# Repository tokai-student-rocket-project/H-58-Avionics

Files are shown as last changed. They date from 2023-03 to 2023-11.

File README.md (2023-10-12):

# H-58 搭載計器





TSRP-H-58に搭載する計器類のプログラム及び設計書を保存するレポジトリです。

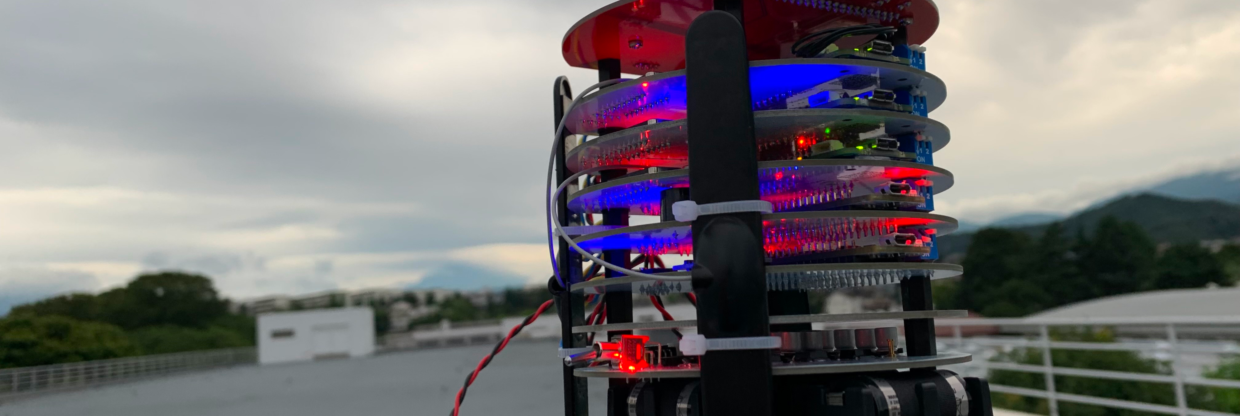
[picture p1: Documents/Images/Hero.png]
Hero


## はじめに

学生ロケットの電装系を盛り上げたい思いから、全てのソースコードを含む設計を公開しています。ガバガバ開発ですので、分かりにくい点（資料がまとまっていないなど）が多々あります。ご了承ください。

ご不明な点は以下のSNSからお気軽にお問合せください。

- X (旧Twitter): [@Tokai_SRP](https://twitter.com/Tokai_SRP)

### 計器の概要

H-58搭載計器はCANBUS接続された複数のモジュールから構成されます。

### レポジトリ構成

#### ./Components/Modules/

- [SystemDataCommunicationModule](./Components/Modules/SystemDataCommunicationModule/README.md)  
- [AirDataCommunicationModule](./Components/Modules/AirDataCommunicationModule/README.md) 
- [FlightModule](./Components/Modules/FlightModule/README.md)  
- [SensingModule](./Components/Modules/SensingModule/README.md) 
- [ValveControlModule](./Components/Modules/ValveContolModule/README.md) 
- [MissionModule](./Components/Modules/MissionModule/README.md) 
- [PowerModule](./Components/Modules/PowerModule/README.md) 

#### ./Documents/

- 開発資料
  - [工程計画書](./Documents/Materials/Schedule.md)
  - [要件定義書](./Documents/Materials/RequirementsDocument.md)
  - [基本設計書](./Documents/Materials/BasicDesignDocument.md)
  - [詳細設計書](./Documents/Materials/DetailedDesignDocument.md)
- 安全審査
  - [一次審査(Z-storage)](https://docs.google.com/document/d/1F-2k9H3952sz7PHYDDPXtUgwHEACfZ0U/edit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)
  - [二次審査(Z-storage)](https://drive.google.com/file/d/1VNDg2A9r9_NxHciDonn3Oh5dWTKx7AV1/view?usp=sharing)
- マニュアル
  - [部品一覧](./Documents/Materials/Manual/PartsList.md)
  - 手順書
    - [組み立て手順書](./Documents/Materials/Manual/Procedure/AssemblyProcedure.md)
- [詳細報告書](./Documents/Reports/DetailedRaport.pdf) (一番情報量多い)

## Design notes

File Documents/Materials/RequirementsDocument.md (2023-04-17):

# 要件定義書

H-58 搭載計器の要件定義、及びシステムの概要について記載する。

## 概要

### 要件

- 海打ち 2 段階分離に対応
- ±200g, 1kHz の加速度計測
- 熱電対による充填確認
- 統合システムとデータバスの実証
- 高速ダウンリンクの実証

### システム構成

- Nucleo-STM32F303K8
- CAN-BUS
- 計測系
  - 加速度/ジャイロ/地磁気
  - クオータニオン
  - 線形加速度
  - 姿勢角
  - 高 g 加速度
  - 気圧
  - 気温
  - 電圧
  - GNSS
- データ処理系
  - 速度算出
  - 高度算出
  - 出力
    - SD カード
    - EEPROM
- 制御系
  - バルブ制御
  - 分離制御
  - フライトモード
  - 状態検知
    - リフトオフ検知
    - 燃焼終了検知
    - 頂点検知
    - 開傘検知
    - 着地検知
- 通信系
  - 1kHz ダウンリンク
  - 慣性情報ダウンリンク
  - 高度情報ダウンリンク
  - 制御情報ダウンリンク
  - 汎用アップリンク
- 電源系
  - 12V パワーライン
  - 5V パワーライン
  - 電池ボックス
  - 変圧基板
  - 12V バルブ電源
- 構造系
  - 計器タワー
  - 水密
  - THR 制御モジュール
  - 搭載カメラ

## モジュール

従来の共通計器, テレメータの統合を行い、各機能をモジュールとして分割して開発を行う。

システムを構成するモジュールは以下の通りである。

- 計測モジュール
- 飛翔管理モジュール
- 通信モジュール
- THR 制御モジュール

各モジュールはプロセッサとして Nucleo-STM32F303K8 を積む。また、各モジュールは CAN-BUS を通して通信を行う。

CAN-BUS を使用したモジュール式のシステムとすることで、高い拡張性と疎結合による高い運用性を期待できる。

Nucleo-STM32F303K8 のマイコンである STM32F303 は、H-57 に搭載した Arduino MKR WAN 1310 の ATSAMD21 と比較して特段性能が高いわけではないが、より高性能なマイコンを有する STM シリーズの開発運用経験を蓄積することができる。これに加えて、ATSAMD21 と STM32F303 は同じ ARM コアであるため、プログラムの互換性があり学習コストが低く、Arduino から STM のステップアップとして最適であると考える。

| | ATSAMD21 | STM32F303 |
| --- | --- | --- |
| 動作周波数 | 48MHz | 72MHz |
| ビット数 | 32bit | 32bit |
| コアの数 | シングルコア | シングルコア |
| コアの種類 | ARM® Cortex®-M0+ | ARM® Cortex®-M4 |
| Flash サイズ | 256kB | 64kB |
| RAM サイズ | 32kB | 16kB |
| 接続性 | I²C, LINbus, SPI, UART/USART, USB | CANbus, I²C, IrDA, LINbus, SPI, UART/USART |

## 計測系

GNSS は通信モジュールで行われ、それ以外は計測モジュールで計測する。

計測するデータと計測レートは以下の通りである。

なお、クオータニオン, 線形加速度, 姿勢角はセンサ内で算出される(NDOF=NineDegreesOfFreedom)ため、計測系として扱う。

また、出力データはデータ処理系に送り、SD, EEPROM に保存されるほか、通信系に送りダウンリンクする。

| データ | センサ | レート | 出力先 |
| --- | --- | --- | --- |
| 加速度 | BNO055 | 100Hz  | SD, ダウンリンク |
| ジャイロ | BNO055 | 100Hz  | SD, ダウンリンク |
| 地磁気 | BNO055 | 100Hz  | SD, ダウンリンク |
| クオータニオン | BNO055 (NDOF)  | 100Hz  | SD, ダウンリンク |
| 線形加速度 | BNO055 (NDOF)  | 100Hz  | SD, ダウンリンク |
| 姿勢角 | BNO055 (NDOF)  | 100Hz  | SD, ダウンリンク |
| 高 g 加速度 | ADXL375 | 1kHz | EEPROM |
| 気圧 | LPS33HW | 100Hz  | SD, ダウンリンク |
| 気温 | サーミスタ ADC | 2Hz | SD, ダウンリンク |
| 電圧 | ADC | 10Hz | SD, ダウンリンク |
| GNSS | SAM-M8Q | 10Hz | SD, ダウンリンク |

## データ処理系

主に計測系で得たデータを処理する。

### 速度算出

線形加速度を経過時間で積分することで求める。

### 高度算出

計測した気圧と気温、及び打ち上げ前に設定する海面気圧から求める。

### 出力

計測や算出した値は以下の 3 通りの出力先に送信される。

- SD
- EEPROM
- ダウンリンク

基本的に全てのデータを SD に保存するとともに、通信系からダウンリンクで地上に送信する。
海打ちの H-58 では、水没や損傷によるデータロストを防ぐためにダウンリンクに重点を置いている。

高 g 加速度のみ計測レートが大きいため EEOROM に保存する。EEPROM は海打ちで実質弾道落下となり水没した H-49 でもデータの保持に成功している。

データの出力に必要な通信速度は以下の通りである。

| 出力先 | 通信速度  |
| --- | --- |
| SD | 38.4 kbps |
| EEPROM | 48 kbps |
| ダウンリンク | 38.4 kbps |

なお、通信速度は値を符号なし 8bit 整数 2 つとみて、生のまま送信した場合である。実際は、パケットに Id や CRC が含まれるため、さらに通信速度は必要になる。

ダウンリンクはデータが経由する CAN-BUS と LoRa でそれぞれ必要になる通信速度である。

## 制御系

制御系はバルブ制御と分離制御、内部制御用のフライトモードと状態検知からなる。

### バルブ制御

THR 制御モジュールで行い、GSE のバルブ開閉信号を受信してバルブシステムのサーボモータを制御する。
サーボモータの制御には RS485 通信を使う。

### 分離制御

不知火の電磁弁に分離信号の DC12V を供給することで分離させる。
H-58 では 2 段階分離となるため、不知火 Ⅲ を頂点、不知火 Ⅳ を指定高度で動作させる。

## 通信系

LoRa による搭載計器地上局間の通信を 5 系統用意する。そのうち 2 系統はダウンリンク用、1 系統はアップリンク用である。

通信モジュールのみプロセッサに Nucleo-STM32F303K8 ではなく Arduino MKR WAN 1310 を使用する。

### 1kHz ダウンリンク

燃焼中3秒間程度の1kHz加速度情報を1分程度かけてダウンリンクする

### 慣性情報ダウンリンク

BNO055から出力される慣性データをダウンリンクする

### 高度情報ダウンリンク

気圧や気温、算出された高度データをダウンリンクする

### 制御情報ダウンリンク

フライトモードやステータスなどの制御情報をダウンリンクする

### 汎用アップリンク

地上局からのコマンドを受信する

## 電源系

### 12V パワーライン

Nucleo-STM32F303K8 は VIN に 12V を受け付けるため、電池ボックスが出力する 15V を変圧基板で 12V へ変圧して各モジュールに供給する。

### 5V パワーライン

Arduino MKR WAN 1310 と搭載カメラを制御する Raspberry Pi は駆動に 5V を要するため、変圧基板で 5V へ変圧して供給する。

### 電池ボックス

3V 出力が可能な CR123A を 5 個直列接続して 15V 出力の電池ボックスとする。電池容量が不足する場合は、電池ボックスを並列接続する。

### 変圧基板

複数個の 3 端子レギュレータで電池ボックスが出力する 15V を 12V と 5V に変圧する。

12V パワーラインと 5V パワーラインは外部給電を設けずに、電源投入時にスイッチで電池ボックスと変圧基板を接続する。

### 12V バルブ電源

バルブ駆動用電源は別系統として、外部給電を行う。内部電源と外部電源は THR 制御モジュール内で切り替える。

## 構造系

### 計器タワー

衝撃に耐えるために、スペーサーを上下のカプラに接続する蓋で固定する両端固定梁の構造とする。
上下の蓋は従来のベークライトではなく、ガラスエポキシを試す。

### 水密

機体チューブの 1 重構造として、上下のカプラ部分に防水用の構造を取り付ける。

### THR 制御モジュール

バルブ制御は燃焼関係の計測を行う THR 制御モジュールの基板は計器タワーではなくバルブ付近に搭載する。

### 搭載カメラ

機体外を撮影するカメラを搭載する。カメラには Raspberry Pi のカメラモジュールを使用する。

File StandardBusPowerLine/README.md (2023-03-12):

# 標準バスパワーライン

ケーブルとコネクタを定めた接続規格です。モジュールの接続に使用します。

## ケーブル

9VとGNDの電源対、CAN_HとCAN_Lの信号対からなる4線2対のツイストケーブルを使用します。

## コネクタ

※未定

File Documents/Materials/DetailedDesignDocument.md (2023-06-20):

# 詳細設計書

## 基本設計からの変更点

- 状態確認用のブザーを追加
- [タイマーのコンフィグについて追記](#フライトモード-フライトモジュール)
- [ロジック図を追加](#分離制御-フライトモジュール)
- [アップリンクの誤動作対策を追加](#システムデータ通信モジュール)
- [計器チューブの穴の寸法を追記](#計器チューブ穴寸法)
- [機体間通信実証モジュールを追加](#機体間通信実証モジュール)
- [バルブ制御モジュールを追加](#アクチュエーターバルブ制御モジュール)
- [THR制御モジュールを削除](#機体間通信実証モジュール)

## 概要

### 特徴

#### 新規要素

- モジュール式の統合システム
- データバスの採用
- ±200g, 1kHz の加速度計測
- 熱電対による充填確認
- クオータニオンのリアルタイム算出

#### 強化要素

- Arduinoからステップアップした高性能マイコン
- 表面実装による小型化
- ダウンリンクの速度向上
- GPS取得頻度向上
- 配線の簡略化による運用性向上

#### 修正要素

- 点火前からの計測
- 外気温計測
- 頂点検知の感度調整

### 成功基準
<!-- 特徴毎に成功基準を設定（通信, ○○制御など） -->

| ミッション | ミニマムサクセス | フルサクセス | エクストラサクセス  |
| :---: | :---: | :---: | :---: |
| フライトモード | フライトピン開放で計測開始 | バルブ開信号で計測開始 | コマンドで計測開始  |
| 分離制御 | 強制分離 (タイマー) | 精度向上のための制御情報取得 | 頂点分離 (頂点検知) |
| 1kHz加速度 | 750Hz~で計測 | ダウンリンクの遅延送信 | OPSの計測 |
| 電源系統 | 安定した電力供給 | バッテリー残量の遠隔監視 | 正常な電源切替 |
| 通信系統 | ダウンリンクの受信 | 2Hz以上で受信 | 10Hz以上で受信 |

## システム
<!-- モジュール同士のデータ的な接続をシステム系統図で説明 -->

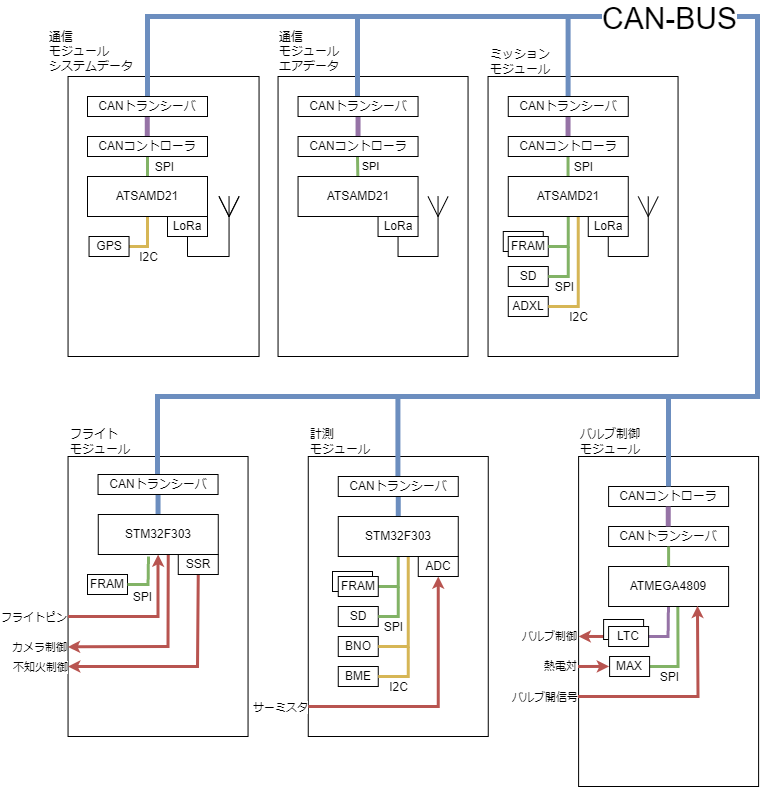
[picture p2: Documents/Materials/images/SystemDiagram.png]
SystemDiagram


### モジュール

従来の共通計器, テレメータの統合を行い、各機能をモジュールとして分割して開発を行う。

システムを構成するモジュールは以下の通りである。

- 計測モジュール ... データ計測, 算出, 保存
- フライトモジュール ... フライトモード管理, 分離制御
- 通信モジュール
  - エアデータ ... 慣性情報, 高度情報のダウンリンク
  - システムデータ ... 制御情報, GNSS情報のダウンリンク, コマンドのアップリンク
- ミッションモジュール ... 1kHz加速度情報の計測, 保存, ダウンリンク
- バルブ制御モジュール ... バルブ制御, 充填確認
- 機体間通信実証モジュール ... CAN通信, 温度

各モジュールはSTM32F303, ATSAMD21, ATSAMD11D14A, ATMega4809のいずれかをマイコンとして搭載しICを介してCAN-BUSに接続する。

### データバス
<!-- CAN-Busの採用とその効果を説明 -->

モジュール間のデータ的な接続のためにCAN-BUSを採用した。CAN-BUSは自動車で広く一般的に使われているデータ通信プロトコルである。通信速度は1Mbpsと必要十分であり、差動式信号のためノイズへの高い耐性を持つ。

データバスの採用により従来の煩雑な配線を減らし、拡張性の高いシステムを構成することができる。また、モジュール間は疎結合となることで、モジュールの開発が容易になり運用性の向上も期待できる。

### データフロー
<!-- データフロー図で説明 -->

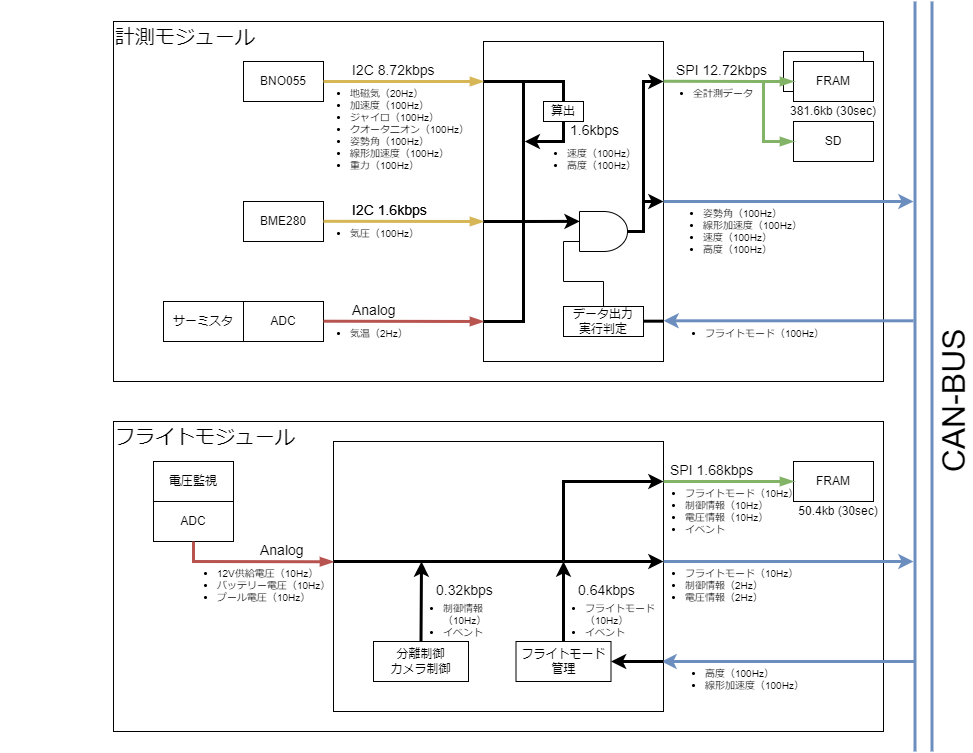
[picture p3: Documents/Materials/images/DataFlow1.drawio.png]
DataFlow1


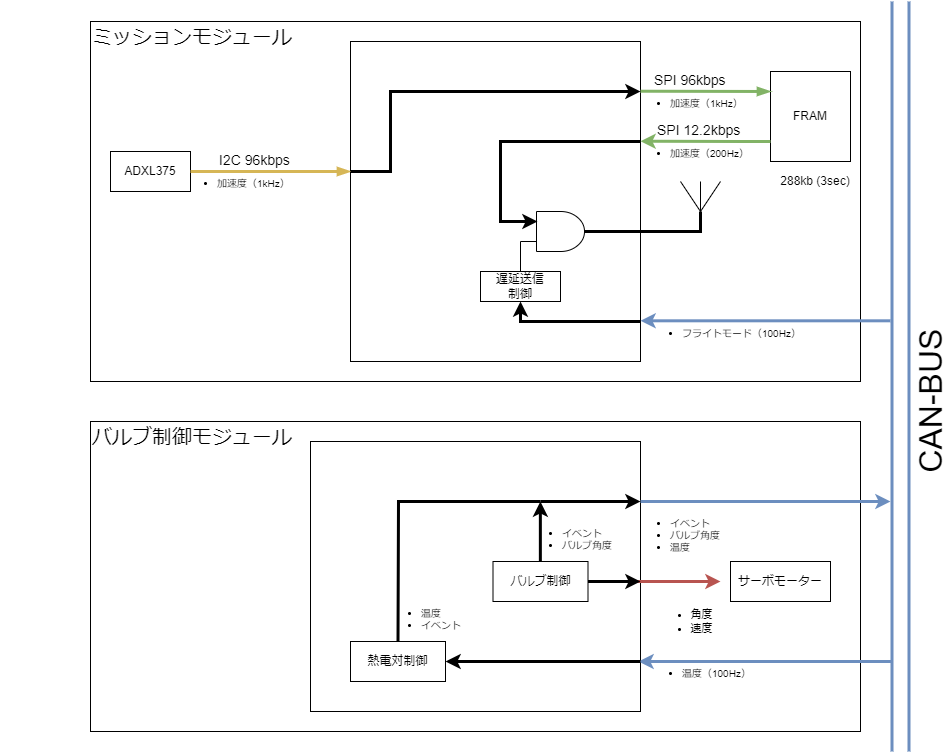
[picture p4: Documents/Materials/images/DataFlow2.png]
DataFlow2


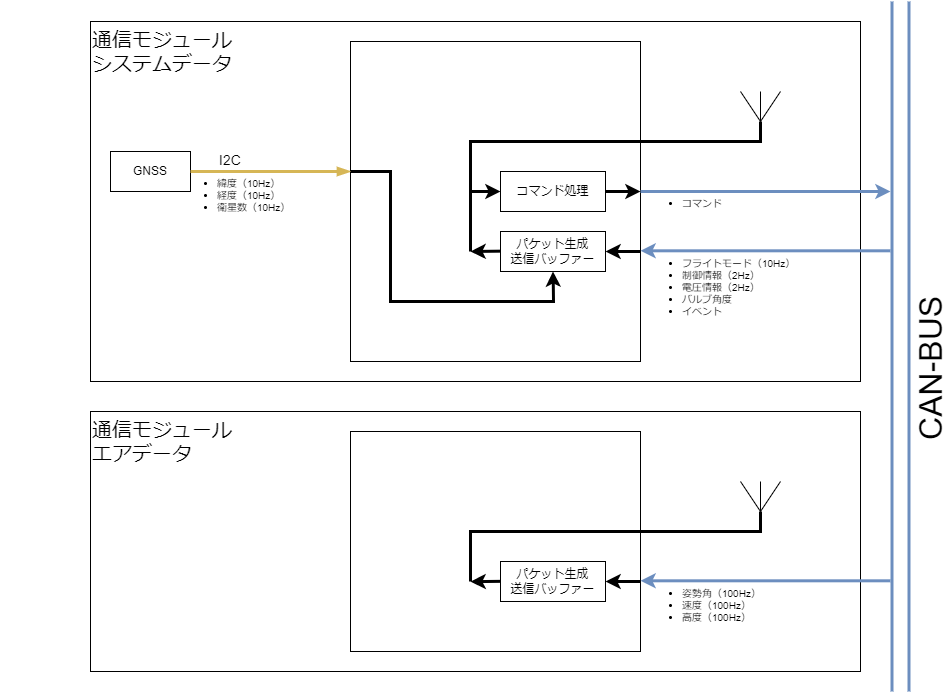
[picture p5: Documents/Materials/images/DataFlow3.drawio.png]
DataFlow3


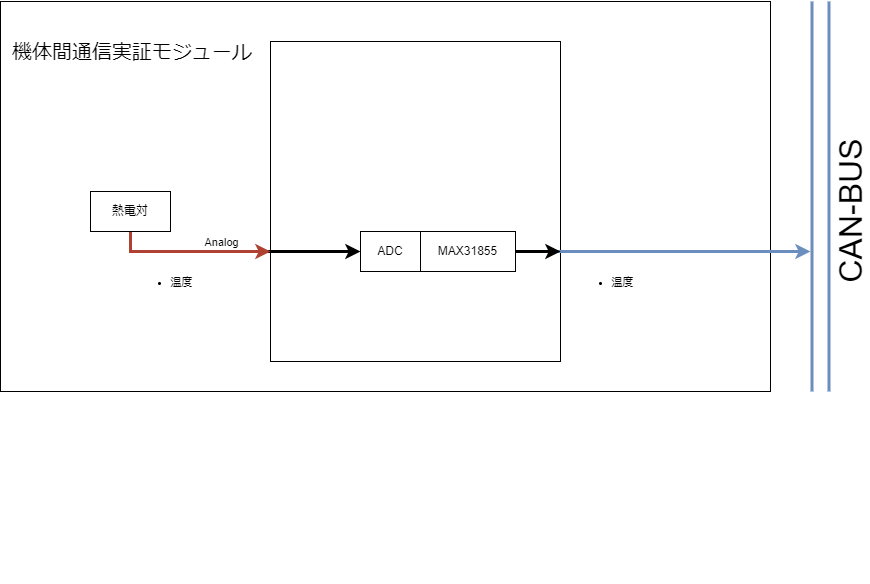
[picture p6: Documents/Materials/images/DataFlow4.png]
DataFlow4


### 電気系統
<!-- 外部給電を含めて電源系統図で説明 -->

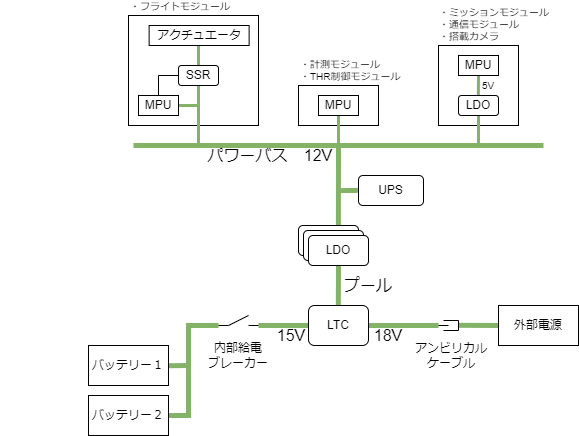
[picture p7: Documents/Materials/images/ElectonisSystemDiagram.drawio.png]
ElectonisSystemDiagram


## 機能

### 計測系

データ保存にはFRAM (Fujitsu MB85RS2MT) とマイクロSDカードを使用する。海打ち仕様として、着水時にFRAMとSDを電気的に遮断することでショートを防止する機構を搭載する。

データ保存はフライトモードオンのタイミングより開始する。 (概ね点火5~10秒前)

#### GNSS情報 (システムデータ通信モジュール)

| データ | センサ  | 出力レート | 出力先 | データ型 | 通信速度 |
| --- | --- | --- | --- | --- | --- |
| 緯度 | SAM-M8Q | 10Hz | ダウンリンク | float | 320bps |
| 経度 | SAM-M8Q | 10Hz | ダウンリンク | float | 320bps |
| 衛星数 | SAM-M8Q | 10Hz | ダウンリンク | int16_t  | 160bps |

#### 慣性情報 (計測モジュール)

| データ | センサ | 出力レート | 出力先 | データ型 | 通信速度 |
| --- | --- | --- | --- | --- | --- |
| 加速度 | BNO055 | 100Hz | FRAM, SD | float * 3axis | 9.6kbps  |
| ジャイロ | BNO055 | 100Hz | FRAM, SD | float * 3axis | 9.6kbps  |
| 地磁気 | BNO055 | 20Hz | FRAM, SD | float * 3axis | 1.92kbps |
| クオータニオン | BNO055 (NDOF) | 100Hz | FRAM, SD | float * 4axis | 12.8kbps |
| 姿勢角 | BNO055 (NDOF) | 100Hz | FRAM, SD, ダウンリンク | float * 3axis | 9.6kbps  |
| 線形加速度 | BNO055 (NDOF) | 100Hz | FRAM, SD, ダウンリンク, 制御系 | float * 3axis | 9.6kbps  |
| 重力 | BNO055 (NDOF) | 100Hz | FRAM, SD | float * 3axis | 9.6kbps  |
| 速度 | 算出 | 100Hz | FRAM, SD, ダウンリンク | float * 3axis | 9.6kbps  |

#### 高度情報 (計測モジュール)

| データ | センサ | 出力レート | 出力先 | データ型 | 通信速度 |
| --- | --- | --- | --- | --- | --- |
| 気圧 | BME280 | 100Hz | FRAM, SD | float | 3.2kbps  |
| 気温 | サーミスタ | 2Hz | FRAM, SD | float | 64bps |
| 高度 | 算出 | 100Hz | FRAM, SD, ダウンリンク, 制御系 | float | 3.2kbps  |

#### 1kHz加速度 (ミッションモジュール)

| データ | センサ  | 出力レート | 出力先 | データ型 | 通信速度 |
| --- | --- | --- | --- | --- | --- |
| 加速度 | ADXL375 | 1kHz | FRAM, ダウンリンク | float * 3axis | 96kbps |

#### 電圧監視 (フライトモジュール)

12V供給, バッテリー電圧, プール電圧を監視する。これにより、遠隔で電池残量の推測や電源の切替状況を監視することができる。

正常値の監視電圧を分圧回路により2.4Vに降圧した後、ADCで電圧を読み取る。これに係数を乗ずることで元の電圧を取得する。

#### 充填監視

| データ | センサ | 出力レート | 出力先 | データ型 | 通信速度 |
| --- | --- | --- | --- | --- | --- |
| 温度 | MAX31855 | 500Hz | ダウンリンク | float | 3.2kbps |

### 制御系

#### フライトモード (フライトモジュール)

状態をフライトモードで管理する。既定の条件を満たすことで次のモードに遷移する。モード遷移時にイベントを発行してダウンリンクで送信する。

バックアップとしてのタイマーはシミュレーションの結果を元に決定する。したがって、打ち上げ当日の早朝と打ち上げ直前に以下のコンフィグをシミュレーション担当と共に作成する。

| | 備考 | H-57の時間(参考) |
| --- | --- | --- |
| モータ作動時間 | | 2,110 ms |
| 分離保護時間 | モータ作動時間からマージン かつ 頂点到達数秒前以内 | 8,196 ms |
| 強制分離時間 | パラが耐えられる対気速度 かつ 頂点到達数秒後以内 | 9,959 ms |
| 着地時間 | 減速落下の場合の時間 | 38,659 ms |
| シャットダウン時間 | 着地時間の数秒程度後 | 43,649 ms |

頂点一段階分離では頂点検知により直接Parachuteモードへ遷移するため、DescentモードとDecelモードは飛ばされる。

| モード | 遷移条件 | 動作 | 備考 |
| --- | --- | --- | --- |
| Sleep | 電源投入 | なにもしない, コマンドは受け付ける | |
| Standby | WakeUpコマンド or Launch信号 (通信不可時) | 計測開始 | フライトモードオン |
| Thrust | 離床検知 | タイマ開始 | |
| Climb | 想定モータ作動時間 | マージン後頂点検知許可 (分離保護時間) | |
| Descent | 頂点検知 | すぐにDecelへ遷移 (頂点分離) | 頂点分離では実質飛ばされる |
| Decel | タイマー (一段目強制分離時間) or 緊急分離コマンド | 一段目分離 | ドローグシュート展開 |
| Parachute | 指定高度到達 or タイマー (二段目強制分離時間) | 二段目分離 | メインシュート展開 |
| Land | タイマー (想定着地時間) | | |
| Shutdown  | タイマー (シャットダウン時間) | 計測終了 | |

#### 離床検知 (フライトモジュール)

フライトピンの離脱による回路切断をプルアップ入力で検知する。チャタリング対策には従来のソフトウェア実装からハードウェア実装に変更した。これにより、発生する遅延を10ミリ秒から2ミリ秒に短縮した。

| 対策前 | 対策後 |
| :---: | :---: |
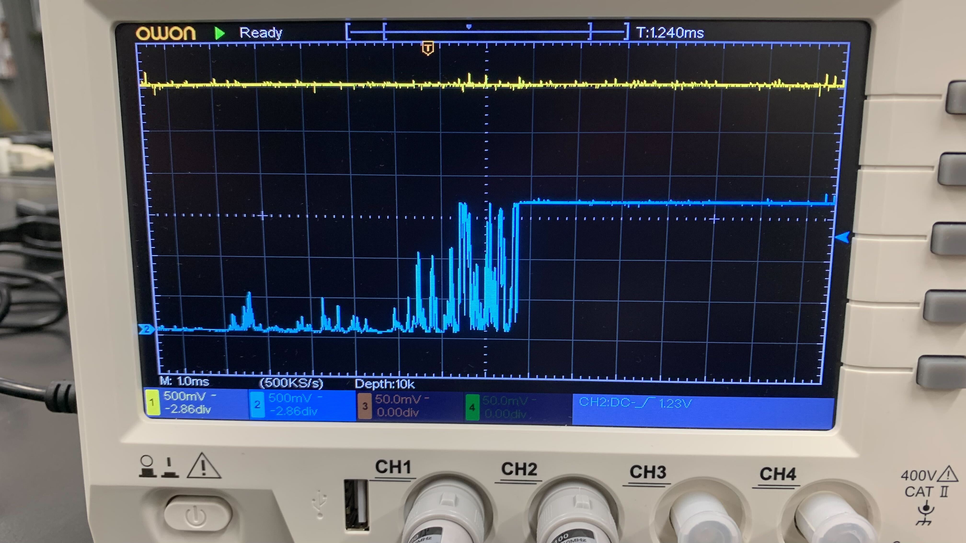
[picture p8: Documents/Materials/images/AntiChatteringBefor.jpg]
AntiChatteringBefor
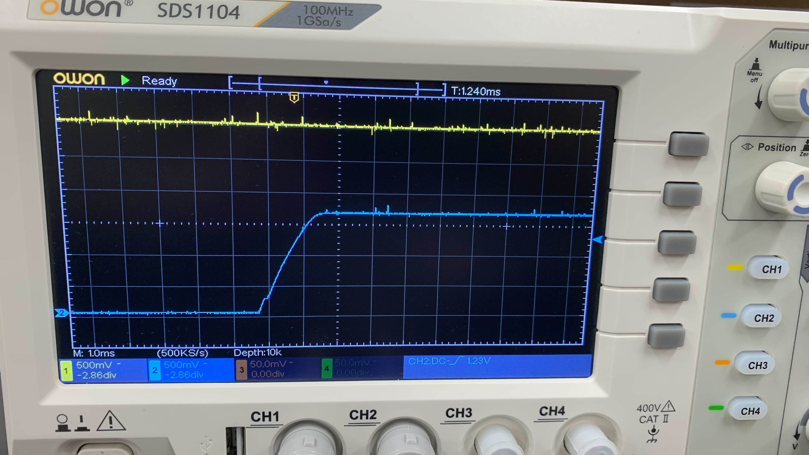
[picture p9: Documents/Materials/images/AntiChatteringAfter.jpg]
AntiChatteringAfter
|  |  |

以下にチャタリング除去回路を示す。

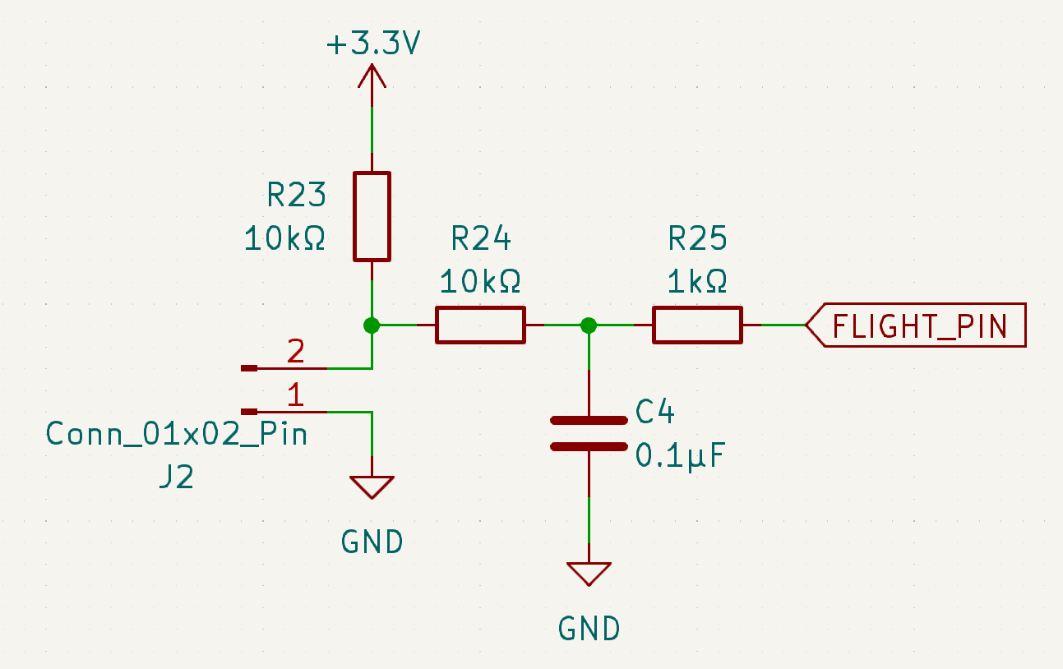
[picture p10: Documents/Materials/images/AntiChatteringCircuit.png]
AntiChatteringCircuit


#### 頂点検知 (フライトモジュール)

H-57で得た改善モデルにより、平滑化定数を0.5とした指数移動平均によって平滑化した高度変化が5回連続で減少したことを検知する。

頂点検知のロジックを以下に示す。

ApogeeDetectionLogic

以下にH-57のフライトデータを例にした頂点検知を示す。初めに連続降下回数を閾値が越えたX+9.57秒後 (実際の頂点到達の0.35秒後) に頂点検知が行われることがわかる。

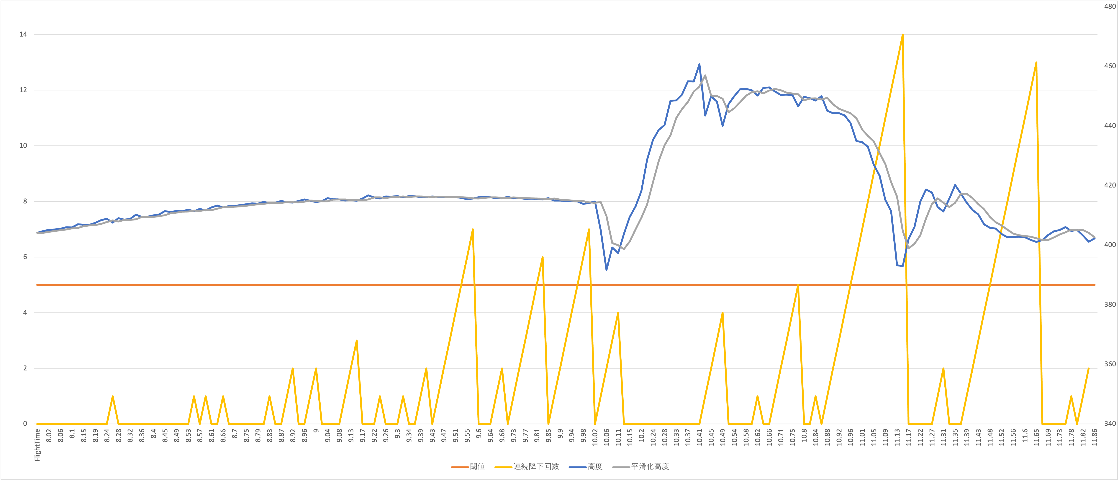
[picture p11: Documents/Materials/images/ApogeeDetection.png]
ApogeeDetection


#### 分離制御 (フライトモジュール)

頂点検知による頂点分離及び、バックアップとしてタイマーによって分離信号を出す。

離床を含めた分離制御のロジックを以下に示す。

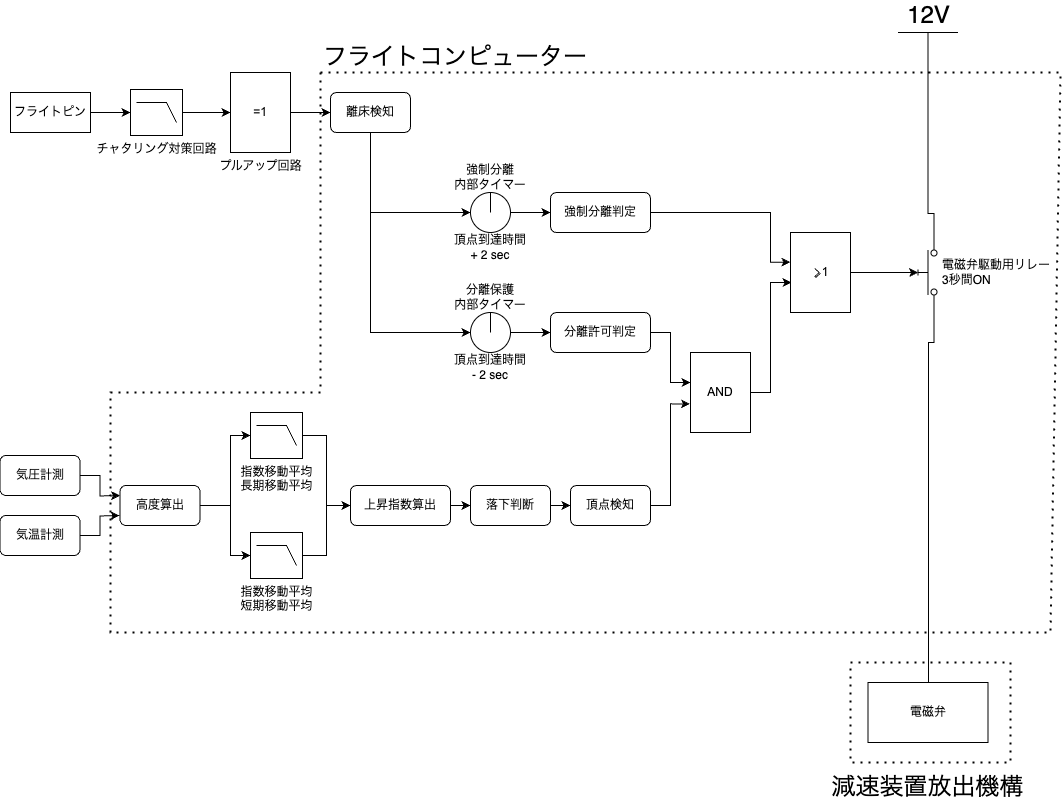
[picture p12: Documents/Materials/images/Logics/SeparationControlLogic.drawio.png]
SeparationControlLogic


制御回路を以下に示す。CONTROL_SEPARATOR_0はマイコンからの3.3V信号であり、分離時には1.65Vに分圧してフォトカプラの1次側に供給する。2次側には別系統の12V電源が接続され、不知火の電磁弁 (HNB1-M5-DC12V) に3秒間12Vを供給する。

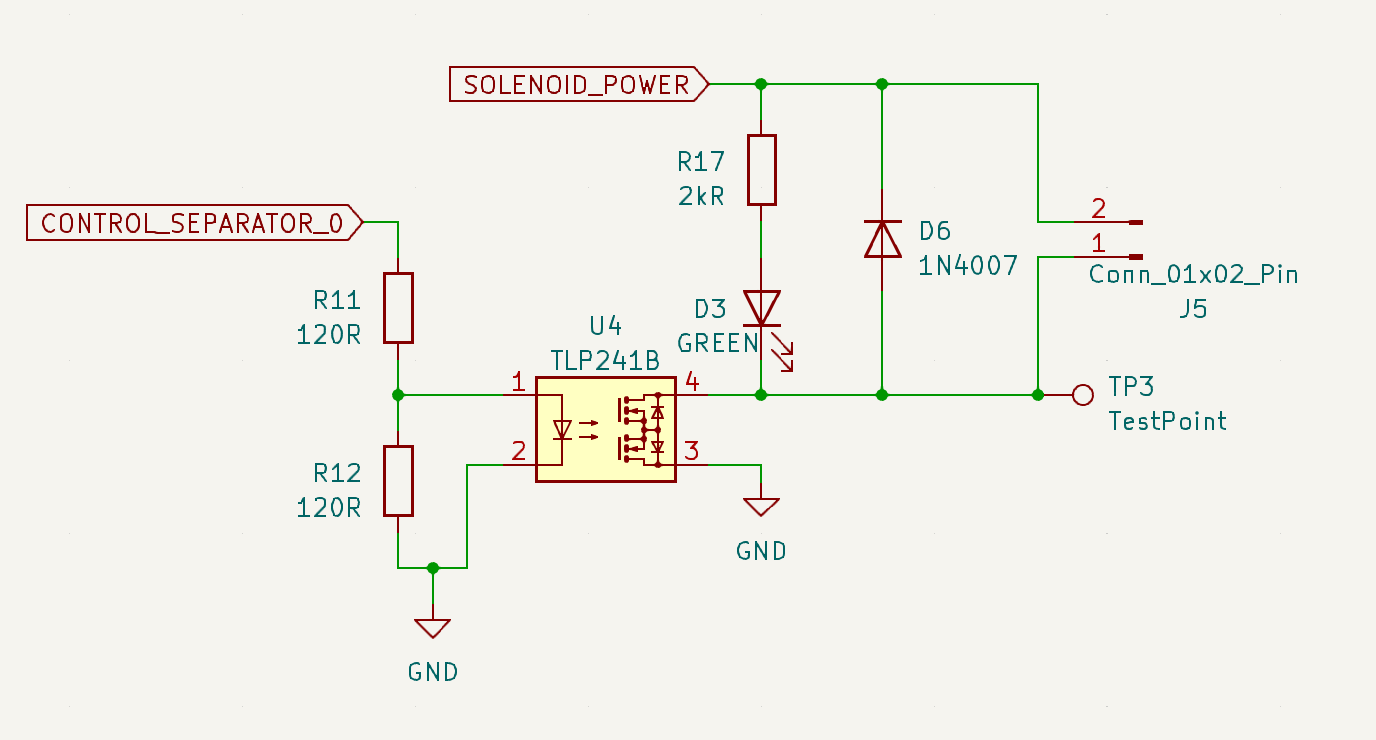
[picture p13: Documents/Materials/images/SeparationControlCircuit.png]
SeparationControlCircuit


#### カメラ制御 (フライトモジュール)

搭載カメラへ録画開始/終了の信号を送る。

録画開始は計測開始と同時、録画終了は動画の保存処理が必要なため想定着地時間の数秒前とする。

### 信号検知（バルブ制御モジュール）

GSEからの信号及びバルブの開閉を検知するためのリミットスイッチをプルアップして検知する。部品数削減のため、プルアップ抵抗は内部プルアップ抵抗を用いる。チャタリング対策として、フライトモジュールと同様のCR回路を採用する。

以下に、チャタリング除去回路を示す。

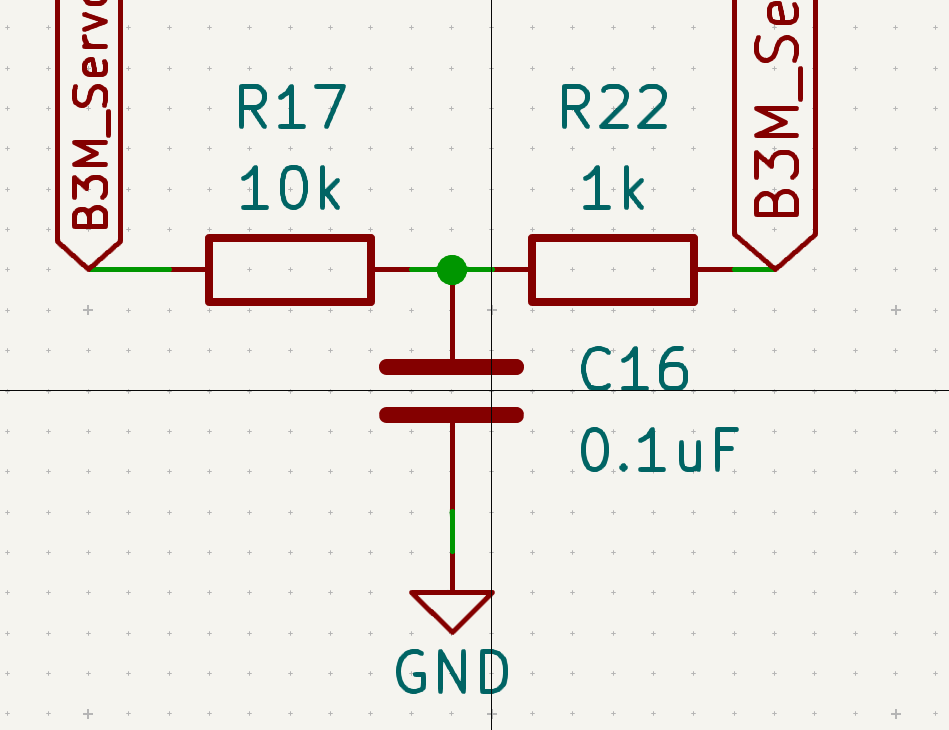
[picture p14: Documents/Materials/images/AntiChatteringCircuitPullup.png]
AntiChatteringCircuitPullup


### 結露対策(機体間通信実証モジュール)

バルブ周辺に搭載するため急激な温度変化が予想される。そこで、結露対策として[ハヤコート Mark2](https://shop.sunhayato.co.jp/products/ay-302)を用い基板表面に絶縁処理が施された被膜を10μm程度になるよう塗布する。
加えて、コネクタやDIP部品の足周りにはホットボンドを用いて結露対策を施す。

### アクチュエーター(バルブ制御モジュール)

H-58に搭載するバルブシステムのアクチュエーターには近藤科学社製[B3M-SC-1170](https://kondo-robot.com/product/03092)を主流路に、[RS405CB](https://www.futaba.co.jp/product/robot/command_type_servos/rs405cb)を供給路に搭載する。

| スペック | B3M-SC-1170 | RS405CB |
| --- | --- | --- |
| 動作電圧 [V] | 6.0 ~ 12.0  | 7.2 ~ 12.0 |
| 最大トルク [Nm] | 7.65 | 4.71 |
| 制御方式 | RS485 | RS485/PWM  |
| 待機電流 [mA] | 68 | 30 |
| 重量 [g] | 105 | 67 |

両者、主な用途がロボット用であるため位置やトルクなど多くの制御が可能なことが特徴。
ハード面でも開栓検知は行っているが、ソフトウェア面でも取り組んでいく。
H-57との変更点としてB3M-SC-1170, RS405CB は共にRS485通信規格によるコマンド方式のサーボであるためPWM制御のサーボモーターと比べて(ソフトウェアをがんばれば)より簡単に速度、角度の制御を実現できるようになっている。

主流路の開検知にはマイクロスイッチを用いたリミットスイッチを搭載する。
スイッチが押された時、主流路が90度回転したこととなり開栓しているかどうかを物理的に判断可能となる。

動作の順番はGSEから信号が届くと供給路側のサーボモーターがまず、動作をし主流路側のサーボモーターが次に動作する。
なお、この動作は第4世代GSE（Panasonic製PLC機）専用設計である。

- LaunchMode: GSEからの信号を受け取ると供給路側が閉栓しその約0.5s後に主流路側が開栓する。

- WaitingMode: GSEからの信号を受け取ると供給路が開栓し主流路側が閉栓する。また、ロケットがランチャに挿入後は基本的にWaitingModeとなっている。

主流路が正常に動作し、リミットスイッチと接触した際にはブザーを鳴らし、最終確認の判断を行いやすいようにする。

### 通信系

無線通信はLoRa920MHz帯を3系統使用する。チャンネルは電波産業会 (ARIB) に従い今後決定する。

#### エアデータ通信モジュール

慣性情報と高度情報を20Hzのダウンリンクで送信する。

#### システムデータ通信モジュール

フライトモード, 制御情報, 電圧情報, GNSS情報を10Hzのダウンリンクで送信する。また、コマンドをアップリンクで受信する。

アップリンクには誤動作対策として、CRCによる誤り検知とアップリンクパケットのパスワード照合を行う。

#### ミッションモジュール

1kHz加速度情報を50Hzのダウンリンクで送信する。

ダウンリンクの通信速度がボトルネックであるため、計測したデータは一度FRAMに保存して点火から3秒程度分のデータを送信する遅延送信を行う。

#### 機体間通信実証モジュール

バルブ - モータ付近に搭載予定であったTHR制御モジュールから名称と機能を削減し、CAN通信実証モジュールに変更。

- 搭載する機能
  - CAN通信
  - 充填監視
    - 熱電対による温度の変化

- 見送る機能
  - サーボモーター制御

THR制御モジュールの機能はそのままバルブ制御モジュールへと引き継ぐ。

### 電源系

供給した電力をリニアレギュレーターで12Vに降圧した後、CAN-BUSに併設したバスパワーラインを通して各モジュールに分配する。

供給には内部給電と外部給電の経路があり、LTC4416によって選択が行われ外部給電が優先して使用される。外部給電はアンビリカルケーブルを介して地上に設置された安定化電源に接続され、離床時に切り離される。内部給電は3V出力電池の5直列を2並列としたラダー接続であり、大容量化を行った。

電源投入時には内部電源遮断用のブレーカースイッチの操作を要する。

瞬電対策として100μFのハイブリッド導電性高分子アルミニウム個体電解コンデンサを9個搭載することで、1A定電流放電としたとき4.5ミリ秒の瞬電に耐えられる。

## 構造
<!-- 計器タワーやバルブカプラへの搭載部分をCADなどで説明する -->

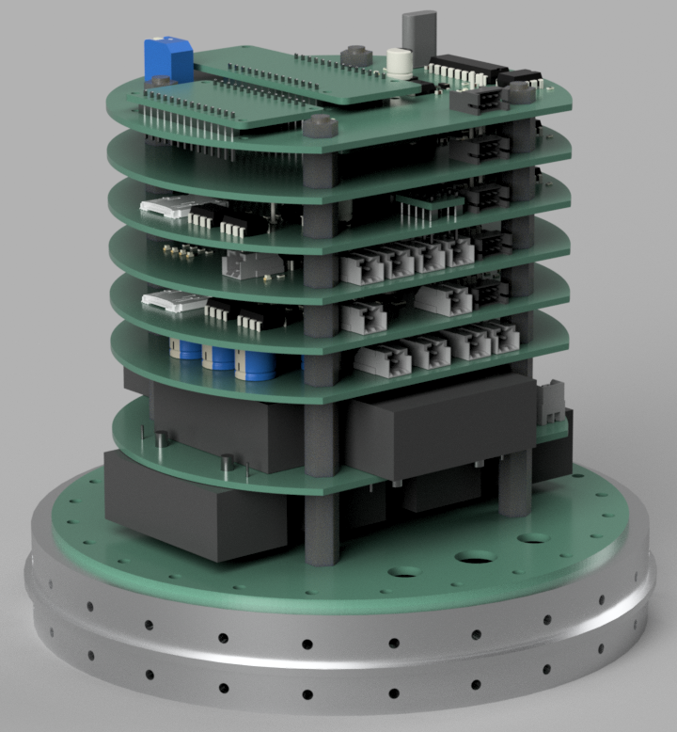
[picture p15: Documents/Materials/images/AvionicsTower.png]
AvionicsTower


計器タワーの高さは搭載カメラを含め160mm程度である。

### 計器チューブ穴寸法

ブレーカースイッチ操作用, アンビリカルケーブル配線用, 搭載カメラ取り付け用として計3箇所の穴が必要である。

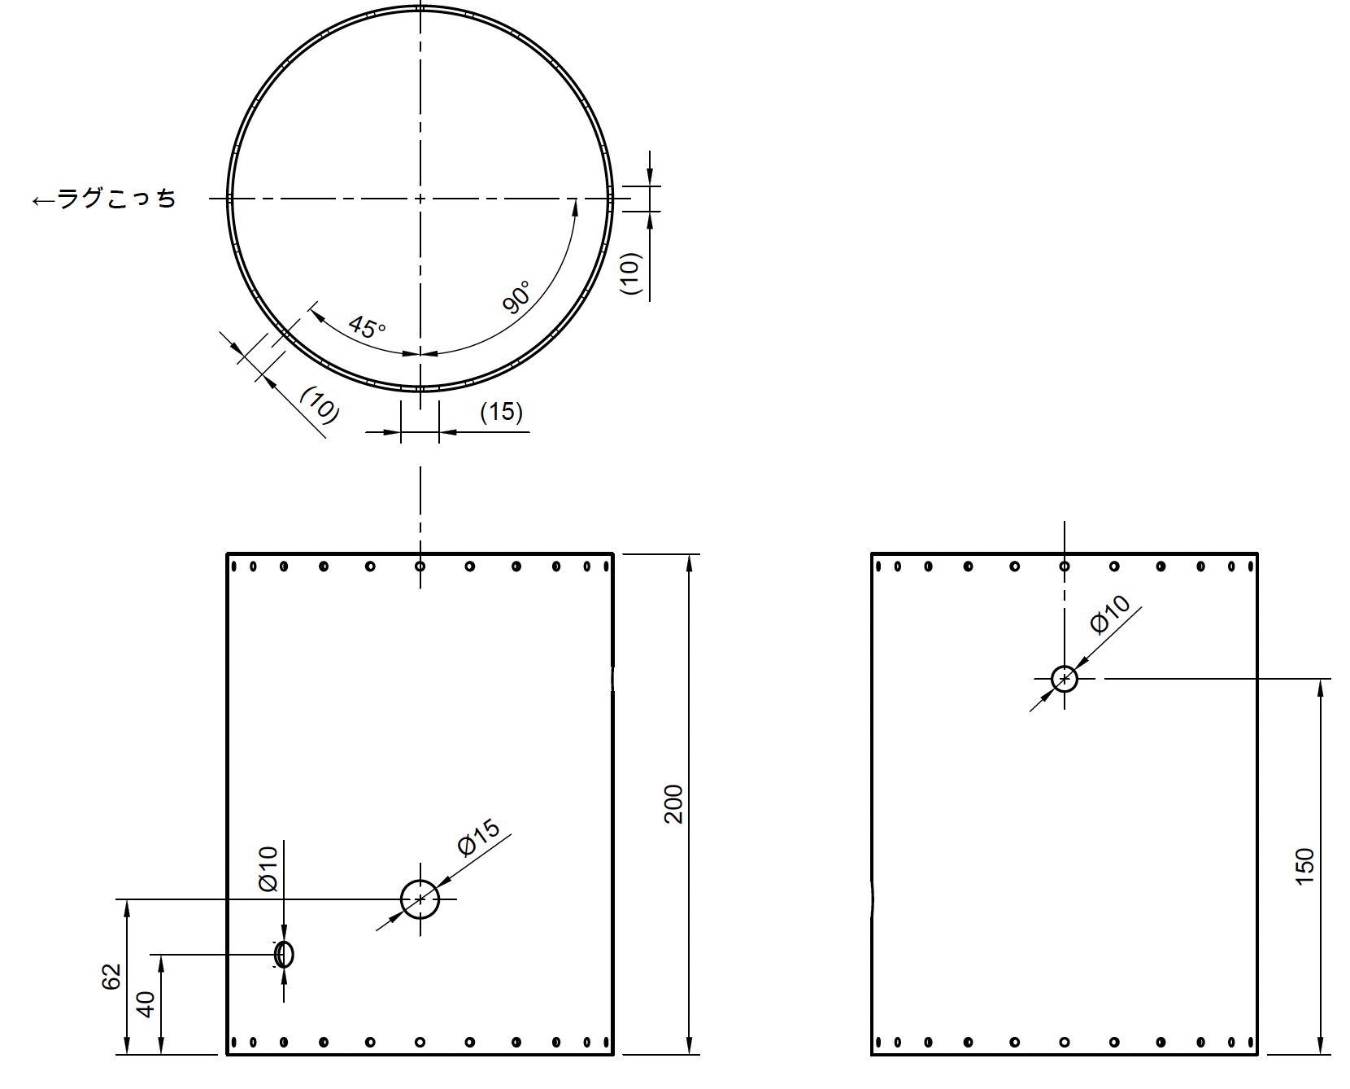
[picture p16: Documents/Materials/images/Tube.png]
Tube


### CANComunicationDemonstrationModule取付穴寸法

取付穴寸法を以下に示す。
EM基板が届いたので取付穴寸法の共有を行う。

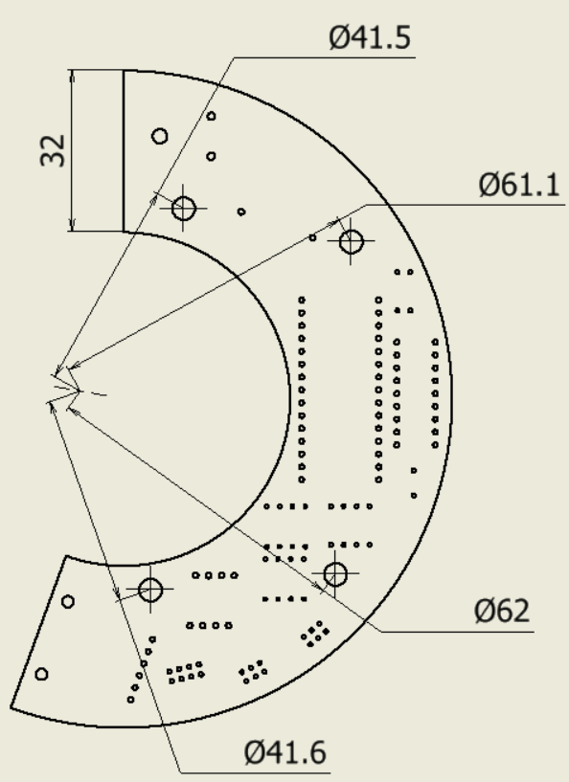
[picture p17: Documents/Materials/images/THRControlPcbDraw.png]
CANComunicationDemonstrationModule


## 配線

### 計器チューブ内

以下に示す各種コネクタを用いて配線を行う。

- ヘッダー
  - [DF11-8DP-2DS(24)](https://www.hirose.com/ja/product/p/CL0543-0535-7-24): 2.0mmピッチ
- ソケット
  - [DF11-8DS-2C](https://www.hirose.com/ja/product/p/CL0543-0503-0-00): 2.0mmピッチ
- 圧着端子
  - [DF11-2428SCF](https://www.hirose.com/ja/product/p/CL0543-0500-2-00): ソケット用端子
  - [DF11EP-2428PCF](https://www.hirose.com/ja/product/p/CL0543-0615-4-00): プラグ用端子

### 計器チューブ内 - 機体間通信実証モジュール

以下に示すコネクタを用いて配線を行う。

- ソケット
  - [DF51-6DS-2C](https://www.hirose.com/ja/product/p/CL0543-5031-0-00): 2.0mmピッチ
- ヘッダー
  - [DF51A-6DP-2DSA](https://www.hirose.com/ja/product/p/CL0543-5044-0-00): 2.0mmピッチ
- 中継プラグ
  - [DF51-6DEP-2C](https://www.hirose.com/ja/product/p/CL0543-5072-0-00): 2.0mmピッチ

### アンビリカルケーブル

以下に示すコネクタを用いて配線を行う。

- ソケット
  - [DF1B-6DS-2.5RC](https://www.hirose.com/ja/product/p/CL0541-0649-3-00): 2.5mmピッチ
- 中継プラグ
  - [DF1BA-6DEP-2.5RC](https://www.hirose.com/product/p/CL0541-0720-6-00): 2.5mmピッチ
- 圧着端子
  - [DF1B-2428PCF](https://www.hirose.com/ja/product/p/CL0541-0664-7-00)

## スケジュール

現在、第一回目のEM基板が完成して動作試験やソフトウェアの実装を進めている。

第二回目の基板発注は6/21に行い、これをFM基板とする予定である。

- 要件定義 ←済
- 概念設計 ←済
- 部分設計 ←済
- モジュール設計 ←済
- システム設計
- 基板設計 ←済
- 基板製造
- 動作試験

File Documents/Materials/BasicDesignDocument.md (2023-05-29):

# 基本設計書

## 概要

### 特徴

#### 新規要素

- モジュール式の統合システム
- データバスの採用
- ±200g, 1kHz の加速度計測
- 熱電対による充填確認
- クオータニオンのリアルタイム算出

#### 強化要素

- Arduinoからステップアップした高性能マイコン
- 表面実装による小型化
- ダウンリンクの速度向上
- GPS取得頻度向上
- 配線の簡略化による運用性向上

#### 修正要素

- 点火前からの計測
- 外気温計測
- 頂点検知の感度調整

### 成功基準
<!-- 特徴毎に成功基準を設定（通信, ○○制御など） -->

| ミッション | ミニマムサクセス | フルサクセス | エクストラサクセス |
| :---: | :---: | :---: | :---: |
| フライトモード | フライトピン開放で計測開始 | バルブ開信号で計測開始 | コマンドで計測開始 |
| 分離制御 | 強制分離 (タイマー) | 精度向上のための制御情報取得 |  頂点分離 (頂点検知) |
| 1kHz加速度 | 最低500Hzで計測 | FRAMでデータ回収 | ダウンリンクの遅延送信 |
| 電源系統 | 安定した電力供給 | バッテリー残量の遠隔監視 | 正常な電源切替 |
| 通信系統 | ダウンリンクの受信 | 2Hz以上で受信 | 10Hz以上で受信 |

## システム
<!-- モジュール同士のデータ的な接続をシステム系統図で説明 -->

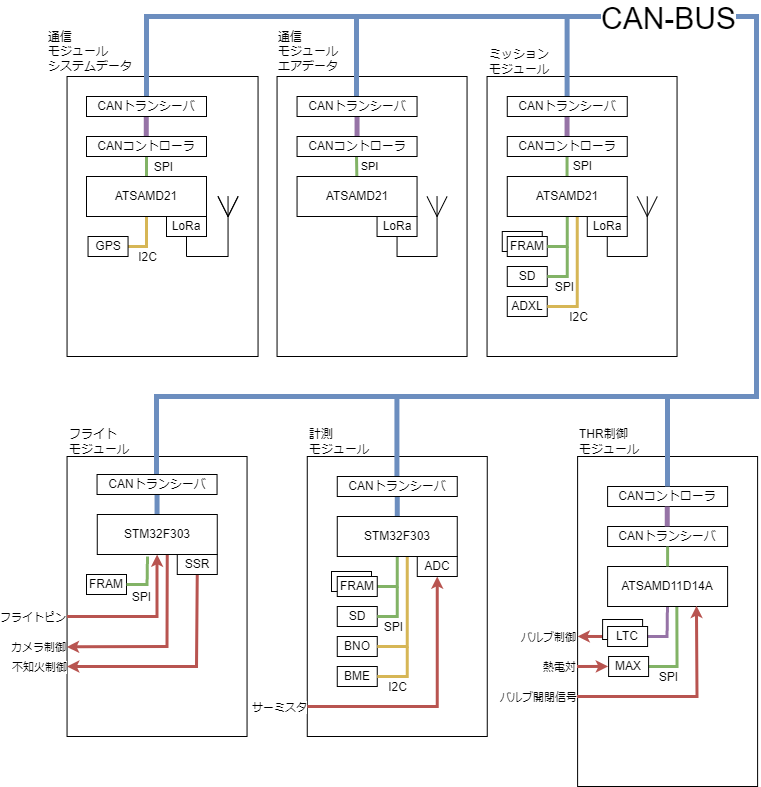
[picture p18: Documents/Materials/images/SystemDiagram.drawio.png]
SystemDiagram


### モジュール

従来の共通計器, テレメータの統合を行い、各機能をモジュールとして分割して開発を行う。

システムを構成するモジュールは以下の通りである。

- 計測モジュール　... データ計測, 算出, 保存
- フライトモジュール ... フライトモード管理, 分離制御
- 通信モジュール
  - エアデータ ... 慣性情報, 高度情報のダウンリンク
  - システムデータ ... 制御情報, GNSS情報のダウンリンク, コマンドのアップリンク
- ミッションモジュール ... 1kHz加速度情報の計測, 保存, ダウンリンク
- THR制御モジュール ... バルブ制御, 充填確認

各モジュールはSTM32F303, ATSAMD21, ATSAMD11D14A, ATMega4809のいずれかをマイコンとして搭載しICを介してCAN-BUSに接続する。

### データバス
<!-- CAN-Busの採用とその効果を説明 -->

モジュール間のデータ的な接続のためにCAN-BUSを採用した。CAN-BUSは自動車で広く一般的に使われているデータ通信プロトコルである。通信速度は1Mbpsと必要十分であり、差動式信号のためノイズへの高い耐性を持つ。

データバスの採用により従来の煩雑な配線を減らし、拡張性の高いシステムを構成することができる。また、モジュール間は疎結合となることで、モジュールの開発が容易になり運用性の向上も期待できる。

### データフロー
<!-- データフロー図で説明 -->

DataFlow1

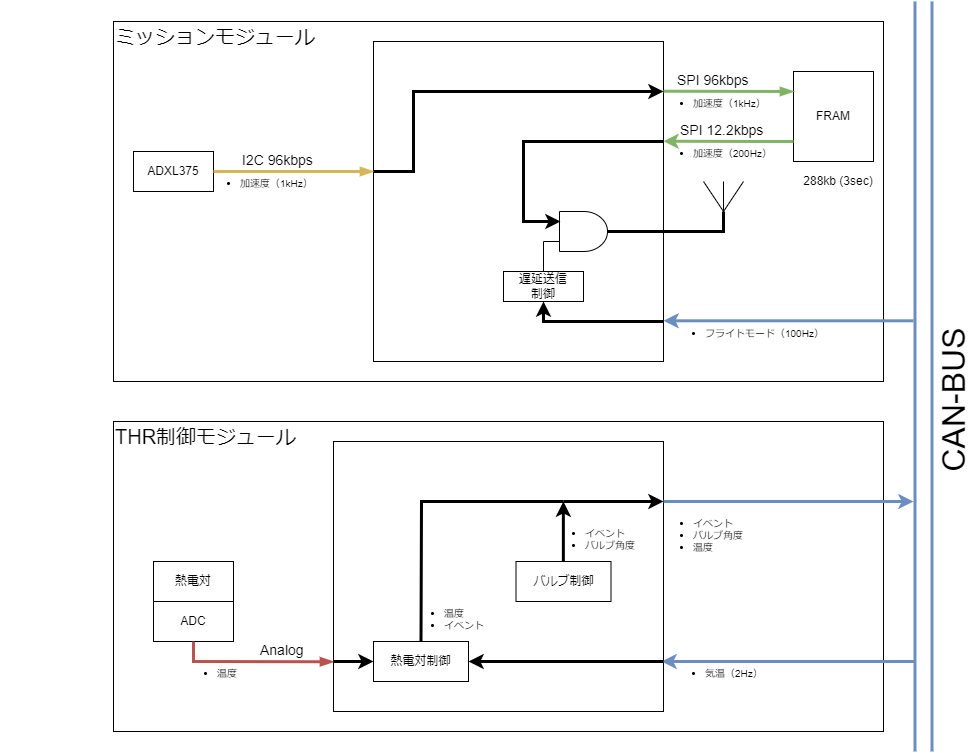
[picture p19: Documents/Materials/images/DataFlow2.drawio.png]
DataFlow2


DataFlow3

### 電気系統
<!-- 外部給電を含めて電源系統図で説明 -->

ElectonisSystemDiagram

## 機能

### 計測系

データ保存にはFRAM (Fujitsu MB85RS2MT) とマイクロSDカードを使用する。海打ち仕様として、着水時にFRAMとSDを電気的に遮断することでショートを防止する機構を搭載する。

データ保存はフライトモードオンのタイミングより開始する。 (概ね点火5~10秒前)

#### GNSS情報 (システムデータ通信モジュール)

| データ | センサ  | 出力レート | 出力先 | データ型 | 通信速度 |
| --- | --- | --- | --- | --- | --- |
| 緯度 | SAM-M8Q | 10Hz | ダウンリンク | float | 320bps |
| 経度 | SAM-M8Q | 10Hz | ダウンリンク | float | 320bps |
| 衛星数 | SAM-M8Q | 10Hz | ダウンリンク | int16_t  | 160bps |

#### 慣性情報 (計測モジュール)

| データ | センサ | 出力レート | 出力先 | データ型 | 通信速度 |
| --- | --- | --- | --- | --- | --- |
| 加速度 | BNO055 | 100Hz | FRAM, SD | float * 3axis | 9.6kbps  |
| ジャイロ | BNO055 | 100Hz | FRAM, SD | float * 3axis | 9.6kbps  |
| 地磁気 | BNO055 | 20Hz | FRAM, SD | float * 3axis | 1.92kbps |
| クオータニオン | BNO055 (NDOF) | 100Hz | FRAM, SD | float * 4axis | 12.8kbps |
| 姿勢角 | BNO055 (NDOF) | 100Hz | FRAM, SD, ダウンリンク | float * 3axis | 9.6kbps  |
| 線形加速度 | BNO055 (NDOF) | 100Hz | FRAM, SD, ダウンリンク, 制御系 | float * 3axis | 9.6kbps  |
| 重力 | BNO055 (NDOF) | 100Hz | FRAM, SD | float * 3axis | 9.6kbps  |
| 速度 | 算出 | 100Hz | FRAM, SD, ダウンリンク | float * 3axis | 9.6kbps  |

#### 高度情報 (計測モジュール)

| データ | センサ | 出力レート | 出力先 | データ型 | 通信速度 |
| --- | --- | --- | --- | --- | --- |
| 気圧 | BME280 | 100Hz | FRAM, SD | float | 3.2kbps  |
| 気温 | サーミスタ | 2Hz | FRAM, SD | float | 64bps |
| 高度 | 算出 | 100Hz | FRAM, SD, ダウンリンク, 制御系 | float | 3.2kbps  |

#### 1kHz加速度 (ミッションモジュール)

| データ | センサ  | 出力レート | 出力先 | データ型 | 通信速度 |
| --- | --- | --- | --- | --- | --- |
| 加速度 | ADXL375 | 1kHz | FRAM, ダウンリンク | float * 3axis | 96kbps |

#### 電圧監視 (フライトモジュール)

12V供給, バッテリー電圧, プール電圧を監視する。これにより、遠隔で電池残量の推測や電源の切替状況を監視することができる。

正常値の監視電圧を分圧回路により2.4Vに降圧した後、ADCで電圧を読み取る。これに係数を乗ずることで元の電圧を取得する。

### 制御系

#### フライトモード (フライトモジュール)

状態をフライトモードで管理する。既定の条件を満たすことで次のモードに遷移する。モード遷移時にイベントを発行してダウンリンクで送信する。

頂点一段階分離では頂点検知により直接Parachuteモードへ遷移するため、DescentモードとDecelモードは飛ばされる。

| モード | 遷移条件 | 動作 | 備考 |
| --- | --- | --- | --- |
| Sleep | 電源投入 | なにもしない, コマンドは受け付ける | |
| Standby | WakeUpコマンド or Launch信号 (通信不可時) | 計測開始 | フライトモードオン |
| Thrust | 離床検知 | タイマ開始 | |
| Climb | 想定モータ作動時間 | マージン後頂点検知許可 (分離保護時間) | |
| Descent | 頂点検知 | すぐにDecelへ遷移 (頂点分離) | 頂点分離では実質飛ばされる |
| Decel | タイマー (一段目強制分離時間) or 緊急分離コマンド | 一段目分離 | ドローグシュート展開 |
| Parachute | 指定高度到達 or タイマー (二段目強制分離時間) | 二段目分離 | メインシュート展開 |
| Land | タイマー (想定着地時間) | | |
| Shutdown  | タイマー (シャットダウン時間) | 計測終了 | |

#### 離床検知 (フライトモジュール)

フライトピンの離脱による回路切断をプルアップ入力で検知する。チャタリング対策には従来のソフトウェア実装からハードウェア実装に変更した。これにより、発生する遅延を10ミリ秒から2ミリ秒に短縮した。

| 対策前 | 対策後 |
| :---: | :---: |
| AntiChatteringBefor | AntiChatteringAfter |

以下にチャタリング除去回路を示す。

AntiChatteringCircuit

#### 頂点検知 (フライトモジュール)

H-57で得た改善モデルにより、平滑化定数を0.5とした指数移動平均によって平滑化した高度変化が5回連続で減少したことを検知する。

以下にH-57のフライトデータを例にした頂点検知を示す。初めに連続降下回数を閾値が越えたX+9.57秒後 (実際の頂点到達の0.35秒後) に頂点検知が行われることがわかる。

ApogeeDetection

#### 分離制御 (フライトモジュール)

頂点検知による頂点分離及び、バックアップとしてタイマーによって分離信号を出す。

制御回路を以下に示す。CONTROL_SEPARATOR_0はマイコンからの3.3V信号であり、分離時には1.65Vに分圧してフォトカプラの1次側に供給する。2次側には別系統の12V電源が接続され、不知火の電磁弁 (HNB1-M5-DC12V) に3秒間12Vを供給する。

SeparationControlCircuit

#### カメラ制御 (フライトモジュール)

搭載カメラへ録画開始/終了の信号を送る。

録画開始は計測開始と同時、録画終了は動画の保存処理が必要なため想定着地時間の数秒前とする。

### 信号検知（THR制御モジュール）

GSEからの信号及びバルブの開閉を検知するためのリミットスイッチをプルアップして検知する。部品数削減のため、プルアップ抵抗は内部プルアップ抵抗を用いる。チャタリング対策として、フライトモジュールと同様のCR回路を採用する。

以下に、チャタリング除去回路を示す。

AntiChatteringCircuitPullup

### 結露対策(THR制御モジュール)

バルブ周辺に搭載するため急激な温度変化が予想される。そこで、結露対策として[ハヤコート Mark2](https://shop.sunhayato.co.jp/products/ay-302)を用い基板表面に絶縁処理が施された被膜を10μm程度になるよう塗布する。

AntiDewCondensationMeasures

使用感が良かった場合、各種モジュールにも塗布することを検討している。これにより基板が生み出すトラブルを未然に防止することが可能となり搭載計器のさらなる信頼性向上が見込める。

### アクチュエーター(THR制御モジュール)

H-58に搭載するバルブシステムのアクチュエーターには近藤科学社製[B3M-SC-1170](https://kondo-robot.com/product/03092)を主流路に、[RS405CB](https://www.futaba.co.jp/product/robot/command_type_servos/rs405cb)を供給路に搭載する。

|スペック| B3M-SC-1170 | RS405CB |
| --- | --- | --- |
| 動作電圧 [V] | 6.0 ~ 12.0 | 7.2 ~ 12.0 |
| 最大トルク [Nm] | 7.65 | 4.71 |
| 制御方式 | RS485 |RS485/PWM|
| 待機電流 [mA] | 68 | 30 |
| 重量 [g]| 105 | 67 |

両者、主な用途がロボット用であるため位置やトルクなど多くの制御が可能なことが特徴。
ハード面でも開閉検知は行っているが、ソフトウェア面でも取り組んでいく。
H-57との変更点としてB3M-SC-1170, RS405CB は共にRS485通信規格によるコマンド方式のサーボであるためPWM制御のサーボモーターと比べて(ソフトウェアをがんばれば)より簡単に速度、角度の制御を実現できるようになっている。

バルブの開閉検知にはマイクロスイッチを用いたリミットスイッチを搭載する。
スイッチが押された時、各種流路が90度回転したこととなり開閉しているかどうかを物理的に判断可能となる。

### 通信系

無線通信はLoRa920MHz帯を3系統使用する。チャンネルは電波産業会 (ARIB) に従い今後決定する。

#### エアデータ通信モジュール

慣性情報と高度情報をダウンリンクで送信する。

#### システムデータ通信モジュール

フライトモード, 制御情報, 電圧情報, GNSS情報をダウンリンクで送信する。また、コマンドをアップリンクで受信する。

#### ミッションモジュール

1kHz加速度情報をダウンリンクで送信する。

ダウンリンクの通信速度がボトルネックであるため、計測したデータは一度FRAMに保存して点火から3秒程度分のデータを200Hzで送信する遅延送信を行う。

### 電源系

供給した電力をリニアレギュレーターで12Vに降圧した後、CAN-BUSに併設したバスパワーラインを通して各モジュールに分配する。

供給には内部給電と外部給電の経路があり、LTC4416によって選択が行われ外部給電が優先して使用される。外部給電はアンビリカルケーブルを介して地上に設置された安定化電源に接続され、離床時に切り離される。内部給電は3V出力電池の5直列を2並列としたラダー接続であり、大容量化を行った。

電源投入時には内部電源遮断用のブレーカースイッチの操作を要する。

瞬電対策として100μFのハイブリッド導電性高分子アルミニウム個体電解コンデンサを9個搭載することで、1A定電流放電としたとき4.5ミリ秒の瞬電に耐えられる。

## 構造
<!-- 計器タワーやバルブカプラへの搭載部分をCADなどで説明する -->

AvionicsTower

計器タワーの高さは搭載カメラを含め142.2mmである。

ブレーカースイッチ操作用として下に示す位置に穴が必要である。

Tube

**THRControlModule取付穴寸法**

取付穴寸法を以下に示す。
6月上旬に実際のPCBも届くので実寸して再度取付穴寸法を共有する。

THRControlPcbDraw

## スケジュール

基板設計を終わらせ発注を行うことを優先したため、ソフトウェア側の開発は最低限の進捗。
5/25に基板発注を行ったため、6月上旬には基板製造が終わる。

- 要件定義 ←済
- 概念設計 ←済
- 部分設計 ←済
- モジュール設計 ←済
- システム設計
- 基板設計 ←済
- 基板製造
- 動作試験

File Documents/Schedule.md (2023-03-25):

# 工程計画書

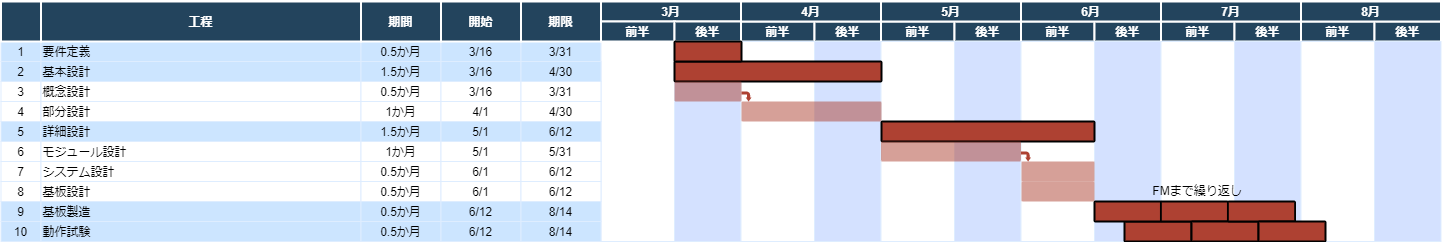
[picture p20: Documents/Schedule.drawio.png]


DRと安全審査の時期が未定なので暫定版

## 工程

### 要件定義

成果物: **要件定義書**  
期限: **3月末**

- ミッションや他班からの要求をまとめる。
- 必要な計測項目や制御項目を洗い出す。

### 基本設計

成果物: **基本設計書**(=issueや各モジュールREADMEのまとめ)  

#### 概念設計

期限: **3月末**

- 具体的な部品や技術の選定

#### 部分設計

期限: **4月末**

- センサや制御部分単位で細分化したBBMを作り、周辺回路やプログラムの実装方法を確認

### 詳細設計

成果物: **詳細設計書**  

#### モジュール設計

期限: **5月末**

- モジュール毎のBBMを作る
- モジュール動作試験

#### システム設計

期限: **6月半ば**

- 全てのモジュールを繋げてシステムとして動かす
- システム動作試験

#### 基板設計

期限: **6月半ば**

- 詳細な回路図, ボード図を作成

### 基板製造

成果物: **EM基板 or FM基板**  
期間: **2週間**

- 基板発注
- 部品実装

### 動作試験

成果物: **運用手順書, 安全審査書**  
期間: **2週間**

- EM基板を試験する
- 問題があれば、設計を修正して**基板製造**から繰り返す
- 問題が無ければ、FM基板に昇格

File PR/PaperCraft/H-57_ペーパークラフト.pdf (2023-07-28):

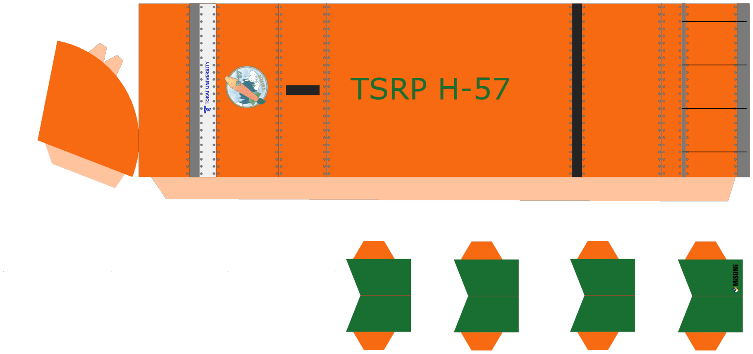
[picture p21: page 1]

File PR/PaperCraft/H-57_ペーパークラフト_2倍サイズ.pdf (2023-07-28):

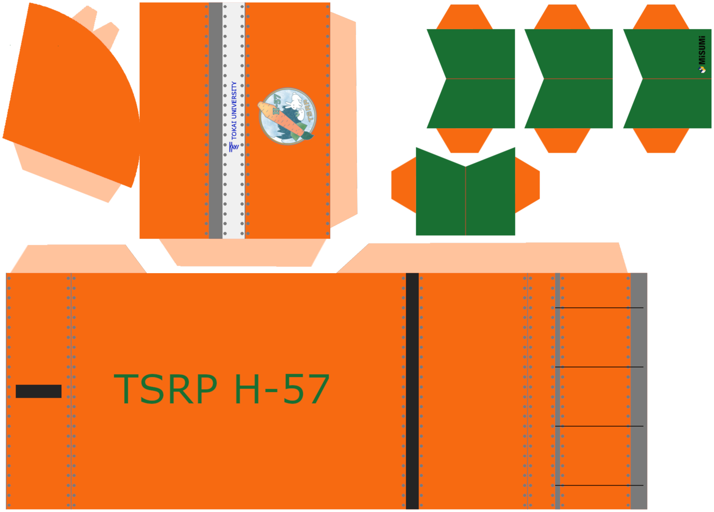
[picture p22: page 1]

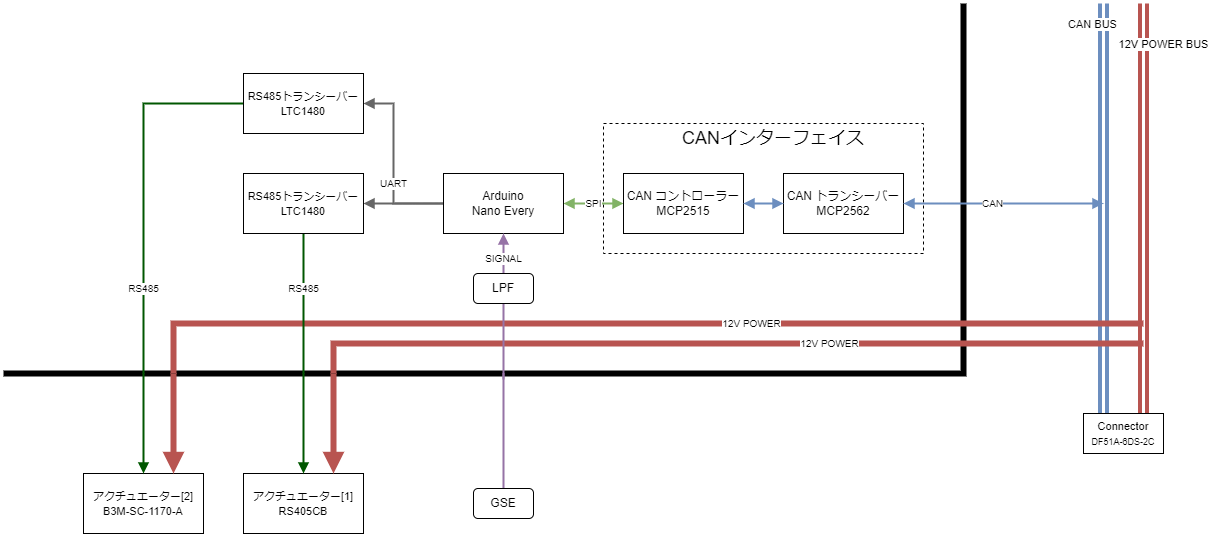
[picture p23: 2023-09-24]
Documents/Reports/Drawio/Images/ValveSystem_BlockDiagram.png

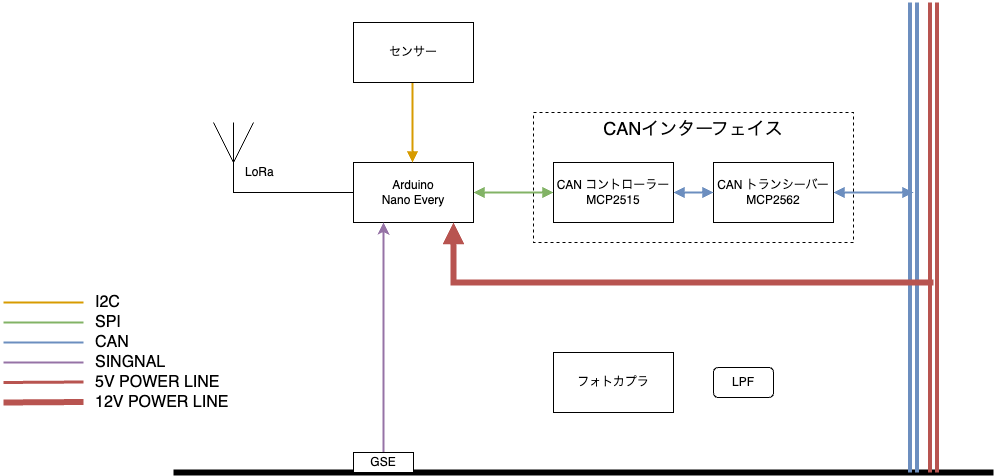
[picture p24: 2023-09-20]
Documents/Reports/Drawio/Images/ColorPalette_BlockDiagram.drawio.png

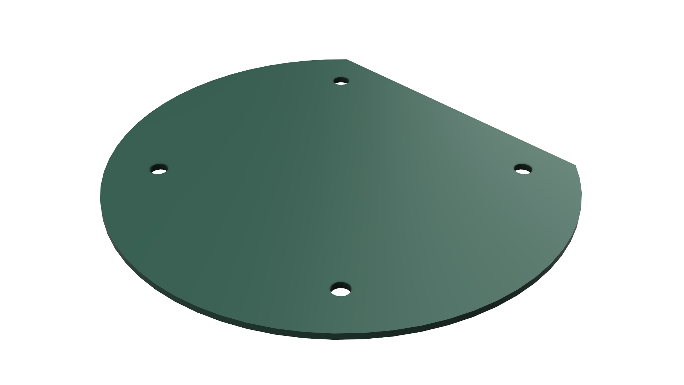
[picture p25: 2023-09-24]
Documents/Reports/images/AvionicsBoard.png

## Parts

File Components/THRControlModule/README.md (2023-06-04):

# THR制御モジュール

バルブ制御、バルブの状態、充填確認をCAN-BUSへ送信し計器タワーに情報を伝える基板です。

## 構成

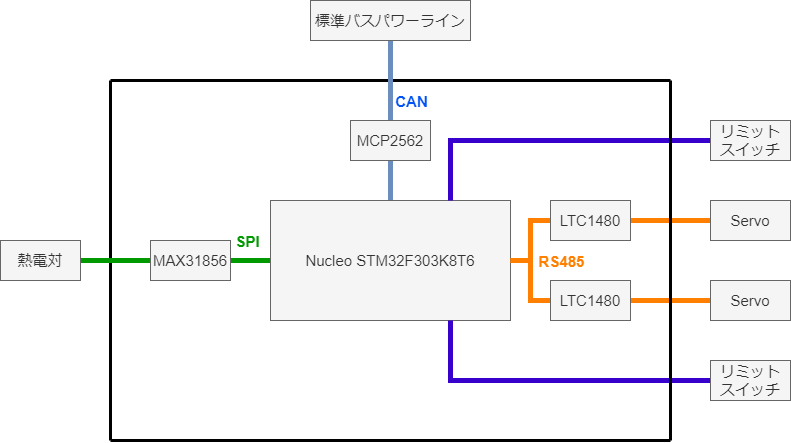
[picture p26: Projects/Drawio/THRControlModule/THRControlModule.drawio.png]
THRControlModule


## 近藤科学B3Mシリーズについて

### B3Mシリーズとは...?

近藤科学様が販売しているシリアル式サーボモーターになります。
高トルク、高耐久のサーボモーターとなります。
制御に使っているライブラリは『ICS Library for Arduino ver.2』を用いています。

> ICS Library for Arduino ver.2のダウンロードは[コチラ](https://kondo-robot.com/faq/ics-library-a2)

### Ics Library for Arduino ver.2 とは…？

近藤科学様が作成している主にKRSシリーズサーボモーターを制御するためのライブラリーです。
使用している関数を流用してB3Mシリーズサーボモーターを制御しています。

> KRSサーボモーターについては[コチラ](https://kondo-robot.com/product-category/servomotor/krs)

### 各種ドキュメント

**ハードウェア**
- [B3Mサーボ](/Documents/Datasheets/B3M/B3M_SoftwareManual1.2.0.3.pdf) [サーボ]

> ブラウザ版は[コチラ](https://kondo-robot.com/w/wp-content/uploads/B3M_SoftwareManual1.2.0.3.pdf)
- [LTC1480](/Documents/Datasheets/LTC1480/j1480_5.pdf) [RS485]

> ブラウザ版は[コチラ](https://www.analog.com/media/jp/technical-documentation/data-sheets/j1480_5.pdf)

- [MAX31855](/Documents/Datasheets/MAX31855/MAX31855_jp.pdf) [デジタルコンバーター]

> ブラウザ版は[コチラ](https://www.analog.com/media/en/technical-documentation/data-sheets/MAX31855.pdf)

- [MAX31856](/Documents/Datasheets/MAX31856/MAX31856_jp.pdf) [デジタルコンバーター]

> ブラウザ版は[コチラ](https://www.analog.com/jp/products/max31856.html#product-overview)

- [MCP2515](/Documents/) [CAN]

> ブラウザ版は[コチラ](https://akizukidenshi.com/download/ds/microchip/mcp2515_j.pdf)

- [MCP2562](/Documents/) [CAN]

> ブラウザ版は[コチラ](https://akizukidenshi.com/download/ds/microchip/MCP2562FD.pdf)
>

**ソフトウェア**
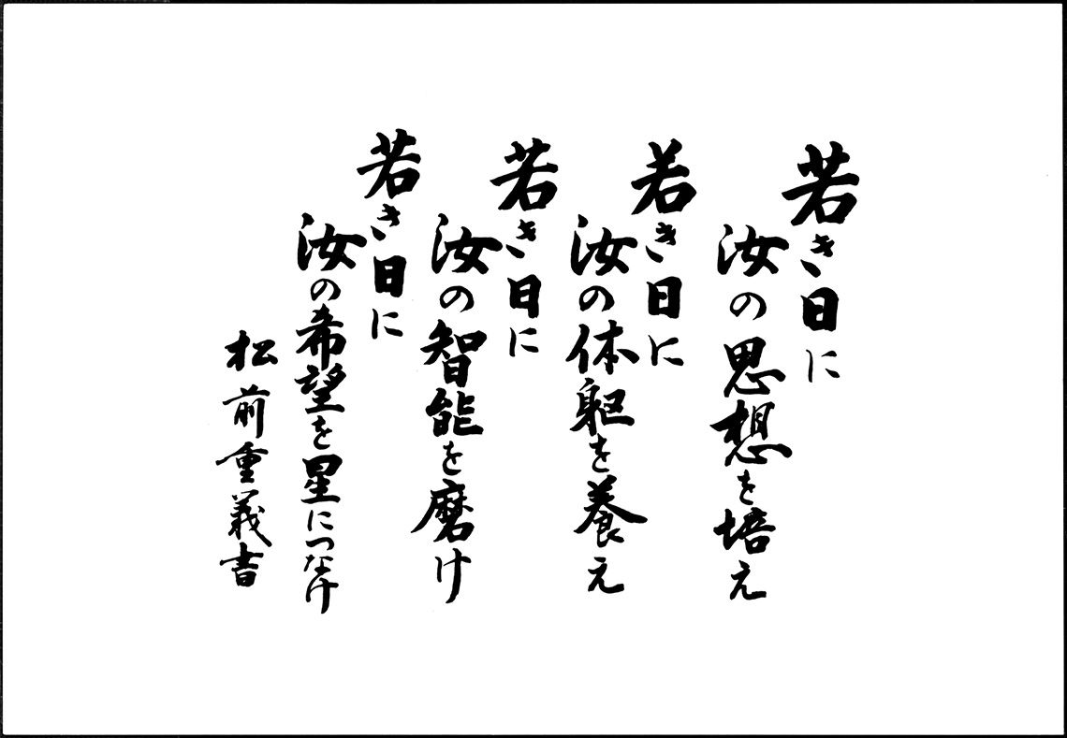
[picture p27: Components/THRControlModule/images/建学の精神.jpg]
建学の精神


### ガバーデータ
- [Experiment Model](/Projects/KiCad/THRControlModuleBoard/Gaber/THRControlModule.zip)(2023/5/25に発注 -> 2023/5/30)
- [Proto Flight Model](/Projects/KiCad/THRControlModuleBoard/)
- [Flight Model](/Projects/KiCad/THRControlModuleBoard/)

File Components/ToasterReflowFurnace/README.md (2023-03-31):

# トースターリフロー炉

## リフロー炉とは？
基板制作において、プリント基板と電子部品をはんだで接着させるための加熱炉として使用されます。
> [こちら](https://metoree.com/categories/4024/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,%E3%81%BE%E3%81%A7%E6%98%87%E6%B8%A9%E3%81%95%E3%82%8C%E3%81%BE%E3%81%99%E3%80%82)で詳しく解説されています。

## 一般的(？)に使われている方法

### 手はんだ

SMD(表面実装)の小さい部品を１つ１つ手作業で実装していく方法。

#### 利点
- はんだごてなどの装備は整っているので用意するものが少ない。

#### 欠点
- 数が多いと難しい。

> ある程度手はんだに慣れている必要がある。パッケージ(外装の種類)によっては職人技。

### ホットプレート
プリント基板にソルダーペーストはんだを塗布し部品を載せてからホットプレートで温める方法。

#### 利点
- ホットプレートさえ用意できれば簡単に実装ができる。

#### 欠点
- ヒーターが下にしかないため、過熱に時間がかかる。
- bottom面の実装が難しい。

> 用意する物も少ないので簡単に挑戦できる。

## トースターリフロー炉

### 利点
- 上下にヒーターがあるため、両面からの過熱が可能。
- 火力(W)がある物を購入できればQOLが上がる。
- 一度にFront面、Bottom面の両方にSMD部品の実装ができる。
- メカから要望のあったCFRP加熱炉を作成する為の前段階として最適な工作。
- 一年生の教育として一緒に作成する題材としても最適(?)。
- 今後、頻繁にSMDの試作基板を作成する場合にあると便利。

### 欠点
- トースターを一台無駄にする。
> はんだなので一度使ったら二度とそのトースターで食品を温められない。(有害)

- AC100Vを若干扱う。
> AC100Vに繋げて作業をしなければ問題ない。

## 準備するもの
- [リフロートースターコントローラーキット](https://www.switch-science.com/products/1690)
> 販売停止品だが回路およびソースコードはオープンソースなので自作できる。
> 団体では１つ所持している。

- DC3.3V出力ACアダプタ
> 3.3V出力できれば大丈夫。3Vでも動作を確認。

- 3.3V対応SSR(ソリッド・ステート・リレー)
  - 対応確認済みのSSR
    - D2425(Crydom)
    - CL240D10(Crydom)
- 5V動作SSR
  - 3.3V => 5Vレベル変換基板をかませば動作させることができるかも。
- 耐熱ケーブル
- いい感じのコネクタ
- 3.3V => 5Vレベル変換基板
- オーブントースター
> 上下2つのヒーターが搭載されているもの

- オーブントースターを分解する勇気

## 参考になった/なりそうな記事
- [なんでも独り言](https://ehbtj.com/electronics/made-reflow-oven/)
- [SWITCH SCIENCE MAGAZINE](https://mag.switch-science.com/2013/10/15/toaster-controller/)

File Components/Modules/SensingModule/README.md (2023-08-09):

# 計測モジュール

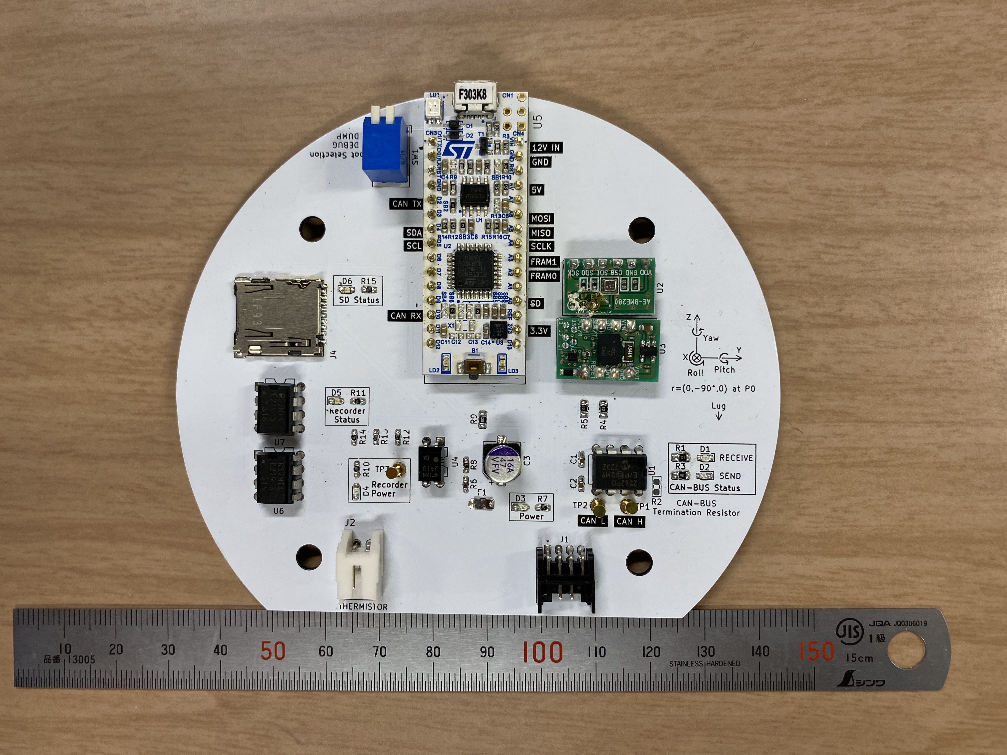
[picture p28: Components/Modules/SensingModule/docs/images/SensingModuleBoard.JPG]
SensingModule


## 概要

計装系サブシステムを担当するモジュール。エアデータを計測するセンサ類、データを保存するメモリ、これらをまとめるマイコンからなる。

### 機能

#### データ計測

センサを利用してデータを計測する。

##### 計測データ一覧

| 計測データ | 使用センサ | 出力レート |
| --- | --- | --- |
| 加速度 | BNO055 | 100Hz |
| 角速度 | BNO055 | 100Hz |
| 地磁気 | BNO055 | 20Hz |
| クオータニオン | BNO055 (NDOF) | 100Hz |
| 姿勢角 | BNO055 (NDOF) | 100Hz |
| 重力加速度 | BNO055 (NDOF) | 100Hz |
| 線型加速度 | BNO055 (NDOF) | 100Hz |
| 気圧 | BME280 | 100Hz |
| 外気温 | サーミスタ | 20Hz |

NDOFとは、BNO055が計測した加速度、角速度、地磁気の9軸から姿勢角など発展的なデータを算出してくれる機能。詳しくは「センサフュージョン」で調べてみてね。

#### データ算出

計測したデータを元に他のデータを算出する。

##### 算出データ一覧

| 算出データ | 使用データ | 出力レート |
| --- | --- | --- |
| 高度 | 気圧, 気温 | 50Hz |
| 上昇率 | 高度 | 50Hz |
| 上昇指数 | 高度 | 50Hz |

上昇指数とは、頂点検知に使用する上昇の勢いを表す値。上昇率が高度変化を微分して算出されるのに対し、上昇指数は高度変化を2種類の指数移動平均にかけた差になっている。

#### 保存

計測したデータや解析用の補助的なデータを保存する。保存先はFRAMとマイクロSDカード。

#### 通信

CANBUSを介して他モジュールと通信する。

### ソフトウェア

ソースコード：[Sources/SensingModule.ino](./Sources/SensingModule/SensingModule.ino)

使用ライブラリ：

- Wire.h ... I2C用
- TaskManager.h ([hideakitai/TaskManager | Github](https://github.com/hideakitai/TaskManager)) ... 定期的に処理を実行するためのライブラリ
- CANSTM ([自作](../../../Libraries/CANSTM/)) ... STMマイコンをCANBUSに接続するためのライブラリ
- BNO055 ([自作](../../../Libraries/BNO055/)) ... 9軸センサBNO055用のライブラリ
- BME280 ([自作](../../../Libraries/BME280/)) ... 気圧センサBME280用のライブラリ
- Thermistor ([自作](../../../Libraries/Thermistor/)) ... サーミスタ用のライブラリ
- Switch ([自作](../../../Libraries/Switch/)) ... プルアップピンを使ったスイッチ用のライブラリ
- LED ([自作](../../../Libraries/LED/)) ... アウトプットピンを使ったLED用のライブラリ
- Trajectory ([自作](../../../Libraries/Trajectory/)) ... 高度算出や上昇率算出など軌道に関する計算用のライブラリ
- Logger ([自作](../../../Libraries/Logger/)) ... FRAMやSDへのデータ保存用ライブラリ
- Var ([自作](../../../Libraries/Var/)) ... 列挙型などの定数を定義したライブラリ

重要な関数は以下の7つ。

- `setup()`
- `loop()`
- `task02Hz()`
- `task2Hz()`
- `task20Hz()`
- `task50Hz()`
- `task100Hz()`

`setup()`は起動時に実行される関数。`loop()`は無限ループして実行される関数。`task○○Hz()`はその周波数で定期的に実行される関数。

詳細な解説は[こちら](./docs/Softwere.md)

### ハードウェア

## 製造

### 発注

ガーバーデータ：[KiCad/Gerber/Build_02/SensingModule.zip](./KiCad/Gerber/Build_02/SensingModule.zip)

Build_01は発注1回目、Build_02は発注2回目。修正版のBuild_02を発注すること。

### 実装

部品表：[KiCad/SensingModule/SensingModule.csv](./KiCad/SensingModule/SensingModule.csv)

### プログラム書き込み

Arduino IDE または Arduino CLI を用いで[ソースコード](./Sources/SensingModule/SensingModule.ino)を書き込む。

## 運用

### 通常運用

**SensingModule.ino**書き込み使用する。

コネクタ類はバスパワーラインとサーミスタを接続する。マイクロSDカードはFRAMとの冗長化のため使用すること。

### データダンプ

**LogDumper.ino**を書き込み使用する。

シリアルポートを接続すると5秒後からデータを出力する。

出力形式はscvでヘッダーはない。

```csv
millis,flightMode,outsideTemperature,pressure,altitude,climbIndex,isFalling,acceleration_x,acceleration_y,acceleration_z,gyroscope_x,gyroscope_y,gyroscope_z,magnetometer_x,magnetometer_y,magnetometer_z,orientation_x,orientation_y,orientation_z,linear_acceleration_x,linear_acceleration_y,linear_acceleration_z,gravity_x,gravity_y,gravity_z,quaternion_w,quaternion_x,quaternion_y,quaternion_z
```

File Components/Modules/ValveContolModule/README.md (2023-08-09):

# バルブ制御モジュール

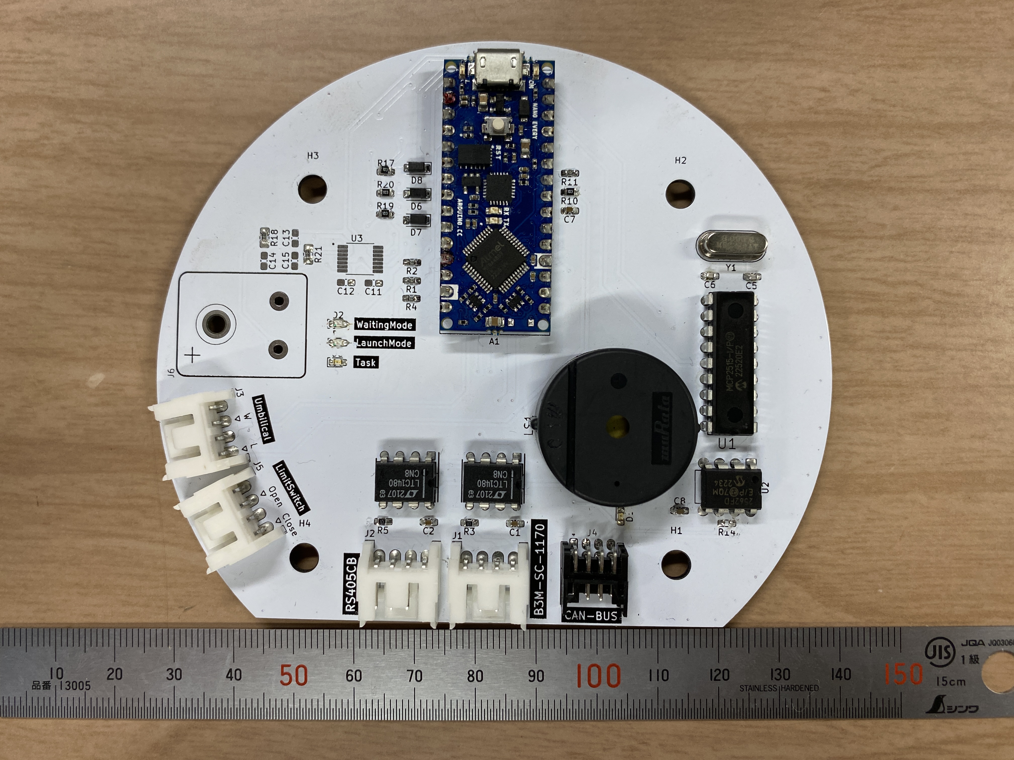
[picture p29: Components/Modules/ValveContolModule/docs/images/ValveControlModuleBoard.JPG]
バルブ制御モジュール


## 概要

### ハードウェア
バルブを制御するために取り付けてあるサーボモータの制御を担当している子．

- **Arduino NANO Every**
  - Arduino NANO Family の一員．
  - Arduino 純正品なので使いやすいが，コンパイルが少し遅い．
  
- **φ110基板**
  - φ150機体にちょうど収まり，配線も行いやすいようになっている．
  - 画像下にある切り欠きは配線をまとめるために工夫を行った．

- **RS485トランシーバーを搭載**
  - サーボモータと通信を行う．

- **ブザーを搭載**
  - 機体内から音で現在の状態を把握することが可能．

- **CAN-BUSを搭載**
  - CAN通信を各モジュール間で行うことで通信量/速度の向上．

### ソフトウェア
プログラム初心者なのでほとんどが拾ってきたもの．
特に，サーボモータを販売している近藤科学さんの[B3MSoftwareManual](../../../Documents/Datasheets/B3M/B3M_SoftwareManual1.2.0.3.pdf)と[B3Mサーボモータを動かそう(Arduino制御編) | 近藤科学](https://kondo-robot.com/faq/b3m_tutorial5r)にとてもお世話になった．

**使用したライブラリ**
- [ICS Library for Arduino ver.2 | 近藤科学](https://kondo-robot.com/faq/ics-library-a2)
  - 別のサーボモータに使用している関数の一部を流用している．
- [TaskManager | Github](https://github.com/hideakitai/TaskManager/tree/master)
  - タスク（行いたい処理）を管理するのにとても便利．例えばある動作を特定の周波数で作動させたいときとか．
- [mcp_2515 | Github](https://github.com/Seeed-Studio/Seeed_Arduino_CAN)
  - CAN通信を担当している[MCP2515](https://akizukidenshi.com/download/ds/microchip/mcp2515_j.pdf)のライブラリ．とても便利．

## パージした機能

- 熱電対による温度計測．
  - 発注した部品が届かなかった．残念．
  - 左側にある大きな四角い形をしたシルクは熱電対の名残．搭載しようとした理由として，センサモジュールではなく，センサを購入してセンサ部を作成してみたかったという理由もある．これにより，手はんだで小さなパッケージのセンサを運用できるのか試してみるという狙いがあった．

## 設計図

### 回路図&ボード図

👉 [ValveControlModule (THRControlModule)](../../../Projects/KiCad/THRControlModule/THRControlModule.kicad_pro)

Kicad ProjectsファイルになっているのでKicadで開けばボード図などもすべて紐づいている．

### 部品表

[THRControlModule.csv](./docs/THRControlModule.csv) を参照のこと．なお，名称がValveControlModuleではなく，THRControlModuleになっている点については触れず，ValveControlModuleに頭の中で置き換えて考えてほしい．(ごめん．)

熱電対部を実装していない関係で以下の表に示す部品は実装しなくてよい．

| Reference | 名称
| -- | -- |
| J6 | K熱電対コネクタ |
| R18 | 100Ω 抵抗 |
| R21 | 100Ω 抵抗 |
| C13, C15 | 0.01μF キャパシタ |
| C11, C12, C14 | 0.1μF キャパシタ|
| U3 | MAX31856 熱電対デジタルコンバータ |
| R17, R19, R20| 10kΩ 抵抗 |
| D6, D7, D8 | 1N4148 ダイオード|

## 製作過程を覗きたい方へ

[Issues | Github](https://github.com/tokai-student-rocket-project/H-58-Avionics/issues)の Close Issues を覗いてほしい．つまずいた箇所や気を付けるべきポイントが多少記載されている．

## つくったひと
 1CES2116 堤 大樹 
 
 ✉ 1ces2116@mail.u-tokai.ac.jp / hiroki1815@outlook.jp / hiroki1815tsutsumi@gmail.com

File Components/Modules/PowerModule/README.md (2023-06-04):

# 電源モジュール

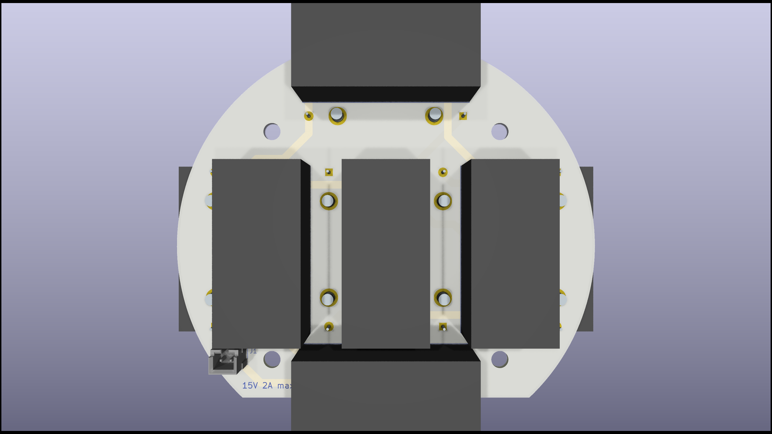
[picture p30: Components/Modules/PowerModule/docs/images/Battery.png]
Battery

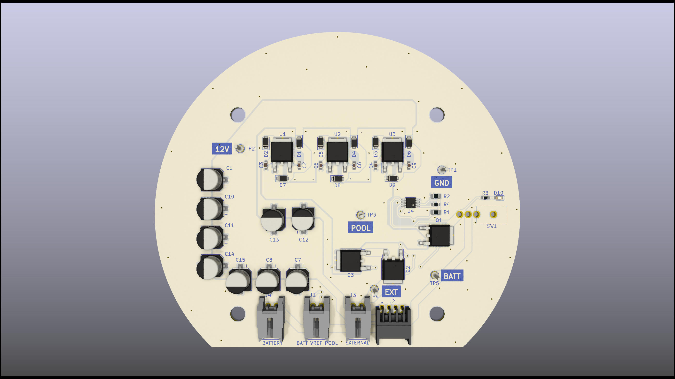
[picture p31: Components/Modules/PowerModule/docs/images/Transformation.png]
Transformation


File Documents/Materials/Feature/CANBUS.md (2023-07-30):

# CANBUS

## パケット一覧

| Id | Label | length | From | To | Rate | Format |
| ---- | --- | --- | ---- | --- | ---- | --- |
| 0x00 | Orientation | 5B | SM | ACM | 20Hz | [0] Axis (uint8_t), [1:5] Value (float) |
| 0x01 | Acceleration | 5B | SM | ACM | 20Hz | [0] Axis (uint8_t), [1:5] Value (float) |
| 0x02 | Altitude | 4B | SM | FM, ACM | 20Hz | [0:4] Value (float) |
| 0x03 | Outside Temperature | 4B | SM | ACM | 20Hz | [0:4] Value (float) |
| 0x04 | Voltage | 6B | FM | SCM | 10Hz | [0:2] Supply Voltage (int16_t), Pool Voltage [2:4] (int16_t), [4:6] Battery Voltage (int16_t) Voltage |
| 0x05 | SystemStatus | 8B | FM | SM, MM, SCM | 10Hz | [0] FlightMode (uint8_t), [1] CameraState (bool), [2] SeparationState (bool), [3] DoLogging (bool), [4:8] FlightTime (uint32_t) |
| 0x06 | Event | 6B | | SCM | | [0] Publisher (uint8_t), [1] EventCode (uint8_t), [2:6] Timestamp (uint32_t) |
| 0x07 | Error | 7B | | SCM | | [0] Publisher (uint8_t), [1] ErrorCode (uint8_t), [2] ErrorReason (uint8_t), [3:7] Timestamp (uint32_t) |
| 0x08 | Set Reference Pressure | 4B | SCM  | SM | | [0:4] ReferencePressure (float) |
| 0x09 | Trajectory Data | 1B | SM | FM | | [0] IsFalling (bool) |
| 0x10 | Sensing Status | 8B | SM | SCM | | [0:4] ReferencePressure (float), [4] IsSystemCalibrated (bool), [5] IsGyroscopeCalibrated (bool), [6] isAccelerometerCalibrated (float), [7] isMagnetometerCalibrated (float) |

SM ... SensingModule  
FM ... FlightModule  
MM ... MissionModule  
ACM ... AirDataCommunicationModule  
SCM ... SystemDataCommunicationModule

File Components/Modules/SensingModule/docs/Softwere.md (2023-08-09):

# ソフトウェア

重要な関数は以下の7つ。

- `setup()`
- `loop()`
- `task02Hz()`
- `task2Hz()`
- `task20Hz()`
- `task50Hz()`
- `task100Hz()`

`setup()`は起動時に実行される関数。`loop()`は無限ループして実行される関数。`task○○Hz()`はその周波数で定期的に実行される関数。

基本的な動作は全て上記の関数に定義されていて、他の関数や変数は上記の関数から呼び出されているだけなので、一旦上記の関数を理解すればいい。

## `setup()`

起動時に実行される関数。
主に初期化処理が書かれている。以下は細分化した解説。

```cpp
  // デバッグ用シリアルポート
  // Serial.begin(115200);
  // while (!Serial);
  // delay(800);
```

デバッグ用のシリアルポートを初期化する処理。
`Serial.print()`などしたかったら、コメントアウトを外す。

```cpp
  // FRAMとSDの電源は常にON
  device::peripheral::recorderPower.on();
```

FRAMとSDへ電源供給を始める処理。
海打ちの際は水没によるショートを防ぐため、着水前に電源供給を止めることができる。H-58は陸打ちなので常にONでいい。

```cpp
  SPI.setMOSI(A6);
  SPI.setMISO(A5);
  SPI.setSCLK(A4);
  SPI.begin();
```

SPI通信を開始する処理。
STM32duinoは使用するピンを明示的に指定しないと動かない仕様。

```cpp
  Wire.setSDA(D4);
  Wire.setSCL(D5);
  Wire.begin();
  Wire.setClock(400000);
```

I2C通信を開始する処理。例によってピンは明示的に指定。クロックは標準的な400kHzにしている。

```cpp
  device::sensor::bno.begin();
  device::sensor::bme.begin();
  device::sensor::thermistor.initialize();
```

センサ類を初期化する処理。
細かい処理は自作のセンサライブラリを参照。

```cpp
  canbus::can.begin();
  canbus::can.sendEvent(CANSTM::Publisher::SENSING_MODULE, CANSTM::EventCode::SETUP);
```

CAN通信を開始する処理。
開始後にはセットアップイベントを発行している。

```cpp
  // CANで送り損ねないように若干ずらしたレートにする
  Tasks.add(internal::task02Hz)->startIntervalSec(5);
  Tasks.add(internal::task2Hz)->startFps(2);
  Tasks.add(internal::task20Hz)->startFps(29);
  Tasks.add(internal::task50Hz)->startFps(53);
  Tasks.add(internal::task100Hz)->startFps(100);
```

後述する定期実行タスクを登録する処理。
FPSが中途半端な値になっているのは、CANにデータを送信する際にタイミングが重なるのを防ぐため。

## `loop()`

無限ループで実行される関数。
以下は細分化した解説。

```cpp
  Tasks.update();
```

タスクを更新する処理。TaskManager.hライブラリで必要。

```cpp
  //CAN受信処理
  if (canbus::can.available()) {
    switch (canbus::can.getLatestMessageLabel()) {
    case CANSTM::Label::SYSTEM_STATUS:
      canbus::handleSystemStatus();
      device::indicator::canReceive.toggle();
      break;
    case CANSTM::Label::SET_REFERENCE_PRESSURE:
      canbus::handleSetReferencePressure();
      device::indicator::canReceive.toggle();
      break;
    }
  }
```

CANの受信処理。

CANを受信したときは、switch文で欲しいデータかを判定して受け取る。計測モジュールでは**SYSTEM_STATUS**と**SET_REFERENCE_PRESSURE**が欲しいデータ。

`canbus::handleSystemStatus()`と`canbus::handleSetReferencePressure()`はデータを受け取った後の具体的な処理がまとめられている。`loop()`の中に長々と処理を書きたくなかったので別にした。

受け取った後はLEDをトグルで切り替えて点滅させる。

## `task02Hz()`

0.2Hzで実行したい処理。

```cpp
  // そんなものはない
```

開発段階で0.2Hzで実行したい処理は消滅した。

## `task2Hz()`

2Hzで実行したい処理。

```cpp
  // SDの検知
  if (device::detection::cardDetection.is(Var::SwitchState::CLOSE)) {
    // SDを検知した時はLED常時点灯
    device::indicator::sdStatus.on();
  }
  else {
    // SDが検知できない時はLED点滅
    device::indicator::sdStatus.toggle();
  }
```

マイクロSDカードの抜き差し検知。

検知できればLEDを常時点灯、検知できなければLEDを点滅させるだけ。

## `task20Hz()`

20Hzで実行したい処理。

```cpp
  // 地磁気はセンサからのODRが20Hzなので20Hzで読み出す
  device::sensor::bno.getMagnetometer(&data::magnetometer_x_nT, &data::magnetometer_y_nT, &data::magnetometer_z_nT);
  // CAN送信が20Hzなので、外気温はそれに合わせて20Hzで読み出す
  device::sensor::thermistor.getTemperature(&data::outsideTemperature_degC);
```

地磁気と外気温の計測。センサから値を取り出すときは基本的に変数をポインタ渡ししている。

## `task50Hz()`

```cpp
  // 気圧と気温から高度を算出する
  // 内部的には落下検知の処理もやっている
  internal::trajectory.update(data::pressure_hPa, data::outsideTemperature_degC);

  data::altitude_m = internal::trajectory.getAltitude();
  data::climbRate_mps = internal::trajectory.getClimbRate();
```

高度算出と上昇率算出。

```cpp
  // CANにデータを流す
  // 安全のため、高度50m以上でないと落下判定しない
  canbus::can.sendTrajectoryData(internal::trajectory.isFalling() && data::altitude_m >= 50.0);
  device::indicator::canSend.toggle();
```

CANに軌道データを送信する

## `task100Hz()`

```cpp
  // BNO055からのデータは基本的に100Hzで読み出す
  device::sensor::bno.getAcceleration(&data::acceleration_x_mps2, &data::acceleration_y_mps2, &data::acceleration_z_mps2);
  device::sensor::bno.getGyroscope(&data::gyroscope_x_dps, &data::gyroscope_y_dps, &data::gyroscope_z_dps);
  device::sensor::bno.getOrientation(&data::orientation_x_deg, &data::orientation_y_deg, &data::orientation_z_deg);
  device::sensor::bno.getLinearAcceleration(&data::linear_acceleration_x_mps2, &data::linear_acceleration_y_mps2, &data::linear_acceleration_z_mps2);
  device::sensor::bno.getGravityVector(&data::gravity_x_mps2, &data::gravity_y_mps2, &data::gravity_z_mps2);
  device::sensor::bno.getQuaternion(&data::quaternion_w, &data::quaternion_x, &data::quaternion_y, &data::quaternion_z);
  // 高度も解析用にできるだけ早い100Hzで読み出したい
  device::sensor::bme.getPressure(&data::pressure_hPa);
```

センサからデータを読み出す

```cpp
  // doLoggingのフラグが立っている時はログを保存する
  // 内部的にはFRAMとSDに書き込んでいる
  if (device::peripheral::logger.isLogging()) {
    device::peripheral::logger.log(
      millis(), static_cast<uint8_t>(data::flightMode),
      data::outsideTemperature_degC, data::pressure_hPa, data::altitude_m, internal::trajectory.climbIndex(), internal::trajectory.isFalling(),
      data::acceleration_x_mps2, data::acceleration_y_mps2, data::acceleration_z_mps2,
      data::gyroscope_x_dps, data::gyroscope_y_dps, data::gyroscope_z_dps,
      data::magnetometer_x_nT, data::magnetometer_y_nT, data::magnetometer_z_nT,
      data::orientation_x_deg, data::orientation_y_deg, data::orientation_z_deg,
      data::linear_acceleration_x_mps2, data::linear_acceleration_y_mps2, data::linear_acceleration_z_mps2,
      data::gravity_x_mps2, data::gravity_y_mps2, data::gravity_z_mps2,
      data::quaternion_w, data::quaternion_x, data::quaternion_y, data::quaternion_z
    );
  }
```

自作のLoggerライブラリを使ってデータを保存する。

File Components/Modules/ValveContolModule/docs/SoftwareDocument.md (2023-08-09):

# ValveControlModule Software Document

## 概要

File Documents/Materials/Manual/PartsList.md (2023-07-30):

# 部品一覧

運用時の部品一覧です。基板実装に必要な部品などは各モジュールのREADMEを参照してください。

## 構造

### 計器ベースプレート

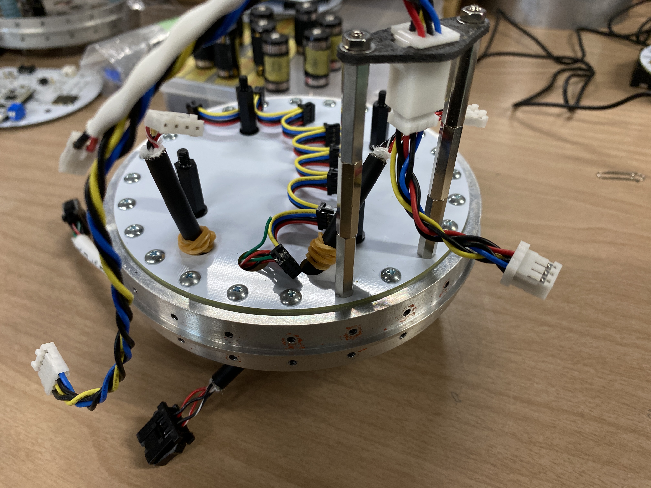
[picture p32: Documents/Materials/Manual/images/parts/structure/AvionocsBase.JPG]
計器ベース


標準カプラに計器ベープレートが締結され、スペーサーとアンビリカルケーブルコネクタパネルが取り付けられた状態。

### 締結部品

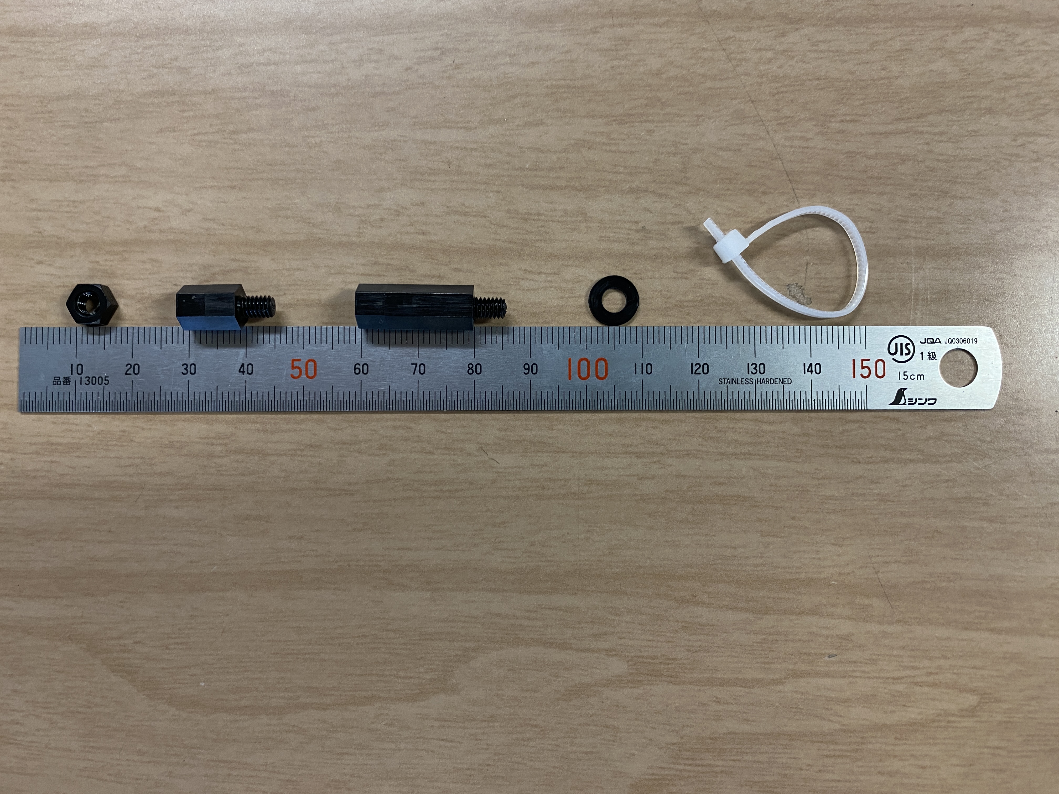
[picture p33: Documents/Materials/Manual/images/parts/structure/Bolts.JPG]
締結部品


左から

- M4 ナット (4個)
- M4x10mm スペーサー (28個)
- M4x20mm スペーサー (4個)
- M4 ワッシャー (24個)
- アンテナ固定用タイラップ (6個)

## 基板

裏面に基板の名称とソースコードへのQRコードが記載されているので参考にしてください。

### 電池ボックス基板

電池ボックス基板

### 変圧基板

変圧基板

### バルブ制御モジュール基板

バルブ制御モジュール基板

### 計測モジュール基板

計測モジュール基板

### フライトモジュール基板

フライトモジュール基板

### ミッションモジュール基板

ミッションモジュール基板

### エアデータ通信モジュール基板

エアデータ通信モジュール基板

### システムデータ通信モジュール基板

システムデータ通信モジュール基板

### カメラモジュール基板

カメラモジュール基板

## 配線

VREF

UmbilicalConnector,CAMERA,SN3

### VREF

電源基板の各点電圧をフライトモジュールから監視するための配線。

### SN3

不知火への分離信号用配線。

### CAMERA

カメラモジュールへの録画信号用配線。

### アンビリカル中継ケーブル

アンビリカルケーブルコネクタパネルと外部のアンビリカルケーブルを中継する配線。

PowerKey

### 電源キー

変圧モジュールの内部電源の鍵として使う配線。

CakeMamoruKun

### ケーキ守るくん

変圧モジュール内のコンデンサによる再起電圧防止のため、無負荷時はケーキ守るくんを取り付けます。

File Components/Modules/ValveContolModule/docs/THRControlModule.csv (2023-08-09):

Reference | Value | Footprint | Datasheet | A1_MAX | A1_MIN | A1_NOM | A_MAX | A_MIN | A_NOM | Arrow Part Number | Arrow Price/Stock | B_MAX | B_MIN | B_NOM | D1_MAX | D1_MIN | D1_NOM | D2_MAX | D2_MIN | D2_NOM | DESCRIPTION | DMAX | DMIN | DNOM | D_MAX | D_MIN | D_NOM | E1_MAX | E1_MIN | E1_NOM | E2_MAX | E2_MIN | E2_NOM | EMAX | EMIN | ENOM | E_MAX | E_MIN | E_NOM | Height | L1_MAX | L1_MIN | L1_NOM | L_MAX | L_MIN | L_NOM | MANUFACTURER | MAXIMUM_PACKAGE_HEIGHT | MPN | Manufacturer_Name | Manufacturer_Part_Number | Mouser Part Number | Mouser Price/Stock | OC_FARNELL | OC_NEWARK | PACKAGE | PACKAGE_TYPE | PARTREV | PINS
A1 | Arduino_Nano_Every | Module:Arduino_Nano | https://content.arduino.cc/assets/NANOEveryV3.0_sch.pdf
C1-C4, C7-C12, C14 | 0.1u | Capacitor_SMD:C_0603_1608Metric_Pad1.08x0.95mm_HandSolder | ~
C5, C6 | 15p | Capacitor_SMD:C_0603_1608Metric_Pad1.08x0.95mm_HandSolder | ~
C13, C15 | 0.01u | Capacitor_SMD:C_0603_1608Metric_Pad1.08x0.95mm_HandSolder | ~
D1-D3, D5 | LED | LED_SMD:LED_0603_1608Metric_Pad1.05x0.95mm_HandSolder | ~
D4, D6-D8 | D | Diode_SMD:D_SOD-123 | ~
H1-H4 | MountingHole | MountingHole:MountingHole_4.5mm | ~
IC1, IC2 | LTC1480CN8#PBF | LTC1480CN8#PBF:DIP794W53P254L1016H394Q8N | https://www.analog.com/media/en/technical-documentation/data-sheets/1480fa.pdf |  |  |  |  |  |  | LTC1480CN8#PBF | https://www.arrow.com/en/products/ltc1480cn8pbf/analog-devices?region=nac |  |  |  |  |  |  |  |  |  |  |  |  |  |  |  |  |  |  |  |  |  |  |  |  |  |  |  |  | 3.937 |  |  |  |  |  |  |  |  |  | Analog Devices | LTC1480CN8#PBF | 584-LTC1480CN8#PBF | https://www.mouser.co.uk/ProductDetail/Analog-Devices/LTC1480CN8PBF?qs=hVkxg5c3xu8DxKxOuOmmTA%3D%3D
J1-J3, J5 | Conn_01x04 | Hirose_Connector:Hirose_DF1BZ-4P-2.5DS | ~
J4 | Conn_01x08 | Hirose_Connector:Hirose_DF11B-8DP-2DS | ~
J6 | Screw_Terminal_01x02 | MAX31856MUD_T:RS_PRO_611-8157 | ~
JP1, JP2 | SolderJumper_2_Open | Jumper:SolderJumper-2_P1.3mm_Open_Pad1.0x1.5mm | ~
LS1 | PKB24SPCH3601-B0 | PKB24SPCH3601-B0:SPKR_PKB24SPCH3601-B0 |  |  |  |  |  |  |  |  |  |  |  |  |  |  |  |  |  |  |  |  |  |  |  |  |  |  |  |  |  |  |  |  |  |  |  |  |  |  |  |  |  |  |  |  | Murata Electronics | 10.0 mm |  |  |  |  |  |  |  |  |  | March 24, 2017
R1, R2, R4, R7, R9, R11, R13, R16 | 1k | Resistor_SMD:R_0603_1608Metric_Pad0.98x0.95mm_HandSolder | ~
R3, R5, R14 | 120 | Resistor_SMD:R_0603_1608Metric_Pad0.98x0.95mm_HandSolder | ~
R6, R8, R10, R12, R15, R17, R19, R20 | 10k | Resistor_SMD:R_0603_1608Metric_Pad0.98x0.95mm_HandSolder | ~
R18, R21 | 100 | Resistor_SMD:R_0805_2012Metric_Pad1.20x1.40mm_HandSolder | ~
U1 | MCP2515-I/P | MCP2515-I_P:DIP254P762X432-18 |  |  |  |  |  |  |  |  |  |  |  |  |  |  |  |  |  |  | CAN CONTRL |  |  |  |  |  |  |  |  |  |  |  |  |  |  |  |  |  |  |  |  |  |  |  |  |  |  |  | MCP2515-I/P |  |  |  |  | 1439391 | 61K2945 | PDIP-18
U2 | MCP2562-E-P | Package_DIP:DIP-8_W7.62mm | http://ww1.microchip.com/downloads/en/DeviceDoc/25167A.pdf
U3 | MAX31856MUD+T | MAX31856MUD_T:SOP65P640X110-14N |  | None | 0.05 | None | 1.1 | 1.1 | 1.1 |  |  | 0.3 | 0.19 | 0.245 |  |  |  | 0.0 | None | None |  |  |  |  | 5.1 | 4.9 | 5.0 | 4.5 | 4.3 | 4.4 | 0.0 | None | None |  |  | 0.65 | 6.55 | 6.25 | 6.4 |  |  |  |  | 0.7 | 0.5 | 0.6 | Maxim Integrated |  |  |  |  |  |  |  |  |  |  | 0
Y1 | 8MHz | Crystal:Crystal_HC49-4H_Vertical | ~
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

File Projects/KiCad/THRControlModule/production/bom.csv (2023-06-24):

Designator | Footprint | Quantity | Value | LCSC Part #
A1 | Arduino_Nano | 1 | Arduino_Nano_Every
C1, C10, C11, C12, C14, C2, C3, C4, C7, C8, C9 | 0603 | 11 | 0.1u
C13, C15 | 0603 | 2 | 0.01u
C5, C6 | 0603 | 2 | 15p
D1, D2, D3, D5 | 0603 | 4 | LED
D4, D6, D7, D8 | D_SOD-123 | 4 | D
H1, H2, H3, H4 | MountingHole_4.5mm | 4 | MountingHole
IC1, IC2 | DIP794W53P254L1016H394Q8N | 2 | LTC1480CN8#PBF
J1, J2, J3, J5 | Hirose_DF1BZ-4P-2.5DS | 4 | Conn_01x04
J4 | Hirose_DF11B-8DP-2DS | 1 | Conn_01x08
J6 | RS_PRO_611-8157 | 1 | Screw_Terminal_01x02
JP1, JP2 | SolderJumper-2_P1.3mm_Open_Pad1.0x1.5mm | 2 | SolderJumper_2_Open
LS1 | SPKR_PKB24SPCH3601-B0 | 1 | PKB24SPCH3601-B0
R1, R11, R13, R16, R2, R4, R7, R9 | 0603 | 8 | 1k
R10, R12, R15, R17, R19, R20, R6, R8 | 0603 | 8 | 10k
R14, R3, R5 | 0603 | 3 | 120
R18, R21 | 0805 | 2 | 100
U1 | DIP254P762X432-18 | 1 | MCP2515-I/P | MCP2515-I/P
U2 | DIP-8_W7.62mm | 1 | MCP2562-E-P
U3 | SOP65P640X110-14N | 1 | MAX31856MUD+T
Y1 | Crystal_HC49-4H_Vertical | 1 | 8MHz

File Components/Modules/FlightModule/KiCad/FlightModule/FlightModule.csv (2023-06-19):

Source: | /Users/waiwai/Projects/H-58-Avionics/Projects/KiCad/Modules/FlightModule/FlightModule.kicad_sch
Date: | 2023 June 19, Monday 10:01:30
Tool: | Eeschema 7.0.1-0
Generator: | /Applications/KiCad/KiCad.app/Contents/SharedSupport/plugins/bom_csv_grouped_by_value.py
Component Count: | 66
Collated Components:
Item | Qty | Reference(s) | Value | LibPart | Footprint | Datasheet | DNP | MANUFACTURER | MAXIMUM_PACKAGE_HEIGHT | PARTREV | SNAPEDA_PN | STANDARD | Sim.Device | Sim.Pins
1 | 1 | BZ1 | Buzzer | Device:Buzzer | Buzzer_Beeper:Buzzer_12x9.5RM7.6 | ~
2 | 3 | C1, C2, C4 | 0.1uF | Device:C | Capacitor_SMD:C_0603_1608Metric_Pad1.08x0.95mm_HandSolder | ~
3 | 1 | C3 | 47uF | Device:C_Polarized | Capacitor_SMD:CP_Elec_6.3x5.9 | ~
4 | 2 | D1, D2 | BLUE | Device:LED | LED_SMD:LED_0603_1608Metric_Pad1.05x0.95mm_HandSolder | ~
5 | 6 | D3, D4, D11, D12, D13, D14 | GREEN | Device:LED | LED_SMD:LED_0603_1608Metric_Pad1.05x0.95mm_HandSolder | ~
6 | 2 | D5, D10 | RED | Device:LED | LED_SMD:LED_0603_1608Metric_Pad1.05x0.95mm_HandSolder | ~
7 | 2 | D6, D7 | 1N4007 | Diode:1N4007 | Diode_SMD:D_SOD-123F | http://www.vishay.com/docs/88503/1n4001.pdf |  |  |  |  |  |  | D | 1=K 2=A
8 | 1 | J1 | Conn_01x08 | Connector_Generic:Conn_01x08 | Hirose_Connector:Hirose_DF11B-8DP-2DS | ~
9 | 5 | J2, J3, J4, J5, J6 | Conn_01x02_Pin | Connector:Conn_01x02_Pin | Hirose_Connector:Hirose_DF1B | ~
10 | 2 | Q1, Q2 | Q_NPN_BEC | Device:Q_NPN_BEC | Package_TO_SOT_SMD:SC-59_Handsoldering | ~
11 | 5 | R1, R11, R12, R14, R15 | 120R | Device:R | Resistor_SMD:R_0603_1608Metric_Pad0.98x0.95mm_HandSolder | ~
12 | 2 | R2, R7 | 820R | Device:R | Resistor_SMD:R_0603_1608Metric_Pad0.98x0.95mm_HandSolder | ~
13 | 1 | R3 | 4.3kR | Device:R | Resistor_SMD:R_0603_1608Metric_Pad0.98x0.95mm_HandSolder | ~
14 | 1 | R4 | 5.6kR | Device:R | Resistor_SMD:R_0603_1608Metric_Pad0.98x0.95mm_HandSolder | ~
15 | 2 | R5, R6 | 100R | Device:R | Resistor_SMD:R_0805_2012Metric_Pad1.20x1.40mm_HandSolder | ~
16 | 1 | R8 | 750R | Device:R | Resistor_SMD:R_0603_1608Metric_Pad0.98x0.95mm_HandSolder | ~
17 | 1 | R9 | 3kR | Device:R | Resistor_SMD:R_0603_1608Metric_Pad0.98x0.95mm_HandSolder | ~
18 | 3 | R10, R17, R20 | 2kR | Device:R | Resistor_SMD:R_0603_1608Metric_Pad0.98x0.95mm_HandSolder | ~
19 | 5 | R13, R18, R19, R21, R22 | 300R | Device:R | Resistor_SMD:R_0603_1608Metric_Pad0.98x0.95mm_HandSolder | ~
20 | 5 | R16, R26, R27, R30, R31 | 4.7kR | Device:R | Resistor_SMD:R_0603_1608Metric_Pad0.98x0.95mm_HandSolder | ~
21 | 2 | R23, R24 | 10kR | Device:R | Resistor_SMD:R_0805_2012Metric_Pad1.20x1.40mm_HandSolder | ~
22 | 1 | R25 | 1kR | Device:R | Resistor_SMD:R_0603_1608Metric_Pad0.98x0.95mm_HandSolder | ~
23 | 1 | SW1 | SW_DIP_x02 | Switch:SW_DIP_x02 | Button_Switch_THT:SW_DIP_SPSTx02_Piano_10.8x6.64mm_W7.62mm_P2.54mm | ~
24 | 6 | TP1, TP2, TP3, TP4, TP5, TP6 | TestPoint | Connector:TestPoint | Connector_Pin:Pin_D1.0mm_L10.0mm | ~
25 | 1 | U1 | MCP2562-E-P | Interface_CAN_LIN:MCP2562-E-P | Package_DIP:DIP-8_W7.62mm | http://ww1.microchip.com/downloads/en/DeviceDoc/25167A.pdf
26 | 1 | U2 | NUCLEO-F303K8 | NUCLEO-F303K8:NUCLEO-F303K8 | NUCLEO-F303K8:MODULE_NUCLEO-F303K8 |  |  | STMicroelectronics | N/A | 5 | NUCLEO-F303K8 | Manufacturer Recommendations
27 | 2 | U3, U4 | TLP241B | Relay_SolidState:TLP222A | Package_DIP:DIP-4_W7.62mm | https://toshiba.semicon-storage.com/info/docget.jsp?did=17036&prodName=TLP222A
28 | 1 | U5 | MB85RS2MT | Memory_NVRAM:MB85RS2MT | Package_DIP:DIP-8_W7.62mm | http://www.fujitsu.com/downloads/MICRO/fsa/pdf/products/memory/fram/MB85RS16-DS501-00014-6v0-E.pdf

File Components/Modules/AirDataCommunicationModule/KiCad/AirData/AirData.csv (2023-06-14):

Source: | /Users/waiwai/Projects/H-58-Avionics/Projects/KiCad/Modules/CommunicationModule/AirData/AirData.kicad_sch
Date: | 2023 June 13, Tuesday 16:18:26
Tool: | Eeschema 7.0.1-0
Generator: | /Applications/KiCad/KiCad.app/Contents/SharedSupport/plugins/bom_csv_grouped_by_value.py
Component Count: | 30
Collated Components:
Item | Qty | Reference(s) | Value | LibPart | Footprint | Datasheet | DNP | DESCRIPTION | MANUFACTURER | MPN | OC_FARNELL | OC_NEWARK | PACKAGE | PARTREV | STANDARD | SUPPLIER | Sim.Device | Sim.Pins
1 | 2 | C1, C7 | 15pF | Device:C | Capacitor_SMD:C_0603_1608Metric_Pad1.08x0.95mm_HandSolder | ~
2 | 1 | C2 | 10uF | Device:C | Capacitor_SMD:C_0603_1608Metric_Pad1.08x0.95mm_HandSolder | ~
3 | 4 | C3, C4, C5, C6 | 0.1uF | Device:C | Capacitor_SMD:C_0603_1608Metric_Pad1.08x0.95mm_HandSolder | ~
4 | 1 | C8 | 47uF | Device:C_Polarized | Capacitor_SMD:CP_Elec_6.3x5.9 | ~
5 | 1 | D1 | RED | Device:LED | LED_SMD:LED_0603_1608Metric_Pad1.05x0.95mm_HandSolder | ~
6 | 4 | D2, D3, D5, D6 | BLUE | Device:LED | LED_SMD:LED_0603_1608Metric_Pad1.05x0.95mm_HandSolder | ~
7 | 1 | D4 | 1N4007 | Diode:1N4007 | Diode_SMD:D_SOD-123F | http://www.vishay.com/docs/88503/1n4001.pdf |  |  |  |  |  |  |  |  |  |  | D | 1=K 2=A
8 | 1 | J1 | Conn_01x08 | Connector_Generic:Conn_01x08 | Hirose_Connector:Hirose_DF11B-8DP-2DS | ~
9 | 1 | R1 | 120R | Device:R | Resistor_SMD:R_0603_1608Metric_Pad0.98x0.95mm_HandSolder | ~
10 | 1 | R2 | 620R | Device:R | Resistor_SMD:R_0603_1608Metric_Pad0.98x0.95mm_HandSolder | ~
11 | 1 | R3 | 10kR | Device:R | Resistor_SMD:R_0805_2012Metric_Pad1.20x1.40mm_HandSolder | ~
12 | 4 | R4, R5, R6, R7 | 100R | Device:R | Resistor_SMD:R_0805_2012Metric_Pad1.20x1.40mm_HandSolder | ~
13 | 1 | SW1 | SW_DIP_x02 | Switch:SW_DIP_x02 | Button_Switch_THT:SW_DIP_SPSTx02_Piano_10.8x6.64mm_W7.62mm_P2.54mm | ~
14 | 2 | TP1, TP2 | TestPoint | Connector:TestPoint | Connector_Pin:Pin_D1.0mm_L10.0mm | ~
15 | 1 | U1 | MCP2562-E-P | Interface_CAN_LIN:MCP2562-E-P | Package_DIP:DIP-8_W7.62mm | http://ww1.microchip.com/downloads/en/DeviceDoc/25167A.pdf
16 | 1 | U2 | MCP2515-I/P | MCP2515-I_P:MCP2515-I{slash}P | Package_DIP:DIP-18_W7.62mm |  |  | CAN CONTRL |  | MCP2515-I/P | 1439391 | 61K2945 | PDIP-18 |  |  | MICROCHIP
17 | 1 | U3 | NJM7805SDL1 | Regulator_Linear:L7805 | Package_TO_SOT_SMD:TO-252-2 | http://www.st.com/content/ccc/resource/technical/document/datasheet/41/4f/b3/b0/12/d4/47/88/CD00000444.pdf/files/CD00000444.pdf/jcr:content/translations/en.CD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
18 | 1 | U4 | ABX00012 | ABX00012:ABX00012 | ABX00012:ARDUINO_ABX00012 |  |  |  | Arduino |  |  |  |  | 5 | Manufacturer Recommendations
19 | 1 | Y1 | 8MHz | Device:Crystal | Crystal:Crystal_SMD_HC49-SD | ~

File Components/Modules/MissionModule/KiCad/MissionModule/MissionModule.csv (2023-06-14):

Source: | /Users/waiwai/Projects/H-58-Avionics/Projects/KiCad/Modules/MissionModule/MissionModule.kicad_sch
Date: | 2023 June 13, Tuesday 16:17:26
Tool: | Eeschema 7.0.1-0
Generator: | /Applications/KiCad/KiCad.app/Contents/SharedSupport/plugins/bom_csv_grouped_by_value.py
Component Count: | 50
Collated Components:
Item | Qty | Reference(s) | Value | LibPart | Footprint | Datasheet | DNP | DESCRIPTION | MANUFACTURER | MPN | OC_FARNELL | OC_NEWARK | PACKAGE | PARTREV | STANDARD | SUPPLIER | Sim.Device | Sim.Pins
1 | 2 | C1, C6 | 15pF | Device:C | Capacitor_SMD:C_0603_1608Metric_Pad1.08x0.95mm_HandSolder | ~
2 | 4 | C2, C4, C5, C7 | 0.1uF | Device:C | Capacitor_SMD:C_0603_1608Metric_Pad1.08x0.95mm_HandSolder | ~
3 | 1 | C3 | 10uF | Device:C | Capacitor_SMD:C_0603_1608Metric_Pad1.08x0.95mm_HandSolder | ~
4 | 2 | C8, C9 | 47uF | Device:C_Polarized | Capacitor_SMD:CP_Elec_6.3x5.9 | ~
5 | 2 | D1, D9 | RED | Device:LED | LED_SMD:LED_0603_1608Metric_Pad1.05x0.95mm_HandSolder | ~
6 | 1 | D2 | 1N4007 | Diode:1N4007 | Diode_SMD:D_SOD-123F | http://www.vishay.com/docs/88503/1n4001.pdf |  |  |  |  |  |  |  |  |  |  | D | 1=K 2=A
7 | 4 | D3, D4, D5, D6 | BLUE | Device:LED | LED_SMD:LED_0603_1608Metric_Pad1.05x0.95mm_HandSolder | ~
8 | 2 | D7, D8 | GREEN | Device:LED | LED_SMD:LED_0603_1608Metric_Pad1.05x0.95mm_HandSolder | ~
9 | 1 | F1 | Polyfuse | Device:Polyfuse | Fuse:Fuse_1206_3216Metric_Pad1.42x1.75mm_HandSolder | ~
10 | 1 | J1 | Conn_01x08 | Connector_Generic:Conn_01x08 | Hirose_Connector:Hirose_DF11B-8DP-2DS | ~
11 | 1 | J2 | Micro_SD_Card_Det_Hirose_DM3AT | Connector:Micro_SD_Card_Det_Hirose_DM3AT | Connector_Card:microSD_HC_Hirose_DM3AT-SF-PEJM5 | https://www.hirose.com/product/en/download_file/key_name/DM3/category/Catalog/doc_file_id/49662/?item_id=195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
12 | 3 | R1, R8, R10 | 120R | Device:R | Resistor_SMD:R_0603_1608Metric_Pad0.98x0.95mm_HandSolder | ~
13 | 1 | R2 | 620R | Device:R | Resistor_SMD:R_0603_1608Metric_Pad0.98x0.95mm_HandSolder | ~
14 | 1 | R3 | 10kR | Device:R | Resistor_SMD:R_0805_2012Metric_Pad1.20x1.40mm_HandSolder | ~
15 | 4 | R4, R5, R6, R7 | 100R | Device:R | Resistor_SMD:R_0805_2012Metric_Pad1.20x1.40mm_HandSolder | ~
16 | 3 | R9, R11, R15 | 300R | Device:R | Resistor_SMD:R_0603_1608Metric_Pad0.98x0.95mm_HandSolder | ~
17 | 4 | R12, R13, R14, R16 | 4.7kR | Device:R | Resistor_SMD:R_0603_1608Metric_Pad0.98x0.95mm_HandSolder | ~
18 | 1 | SW1 | SW_DIP_x02 | Switch:SW_DIP_x02 | Button_Switch_THT:SW_DIP_SPSTx02_Piano_10.8x6.64mm_W7.62mm_P2.54mm | ~
19 | 3 | TP1, TP2, TP3 | TestPoint | Connector:TestPoint | Connector_Pin:Pin_D1.0mm_L10.0mm | ~
20 | 1 | U1 | MCP2562-E-P | Interface_CAN_LIN:MCP2562-E-P | Package_DIP:DIP-8_W7.62mm | http://ww1.microchip.com/downloads/en/DeviceDoc/25167A.pdf
21 | 1 | U2 | MCP2515-I/P | MCP2515-I_P:MCP2515-I{slash}P | Package_DIP:DIP-18_W7.62mm |  |  | CAN CONTRL |  | MCP2515-I/P | 1439391 | 61K2945 | PDIP-18 |  |  | MICROCHIP
22 | 1 | U3 | NJM7805SDL1 | Regulator_Linear:L7805 | Package_TO_SOT_SMD:TO-252-2 | http://www.st.com/content/ccc/resource/technical/document/datasheet/41/4f/b3/b0/12/d4/47/88/CD00000444.pdf/files/CD00000444.pdf/jcr:content/translations/en.CD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
23 | 1 | U4 | ADXL375 | StrawberryLinux_ADXL375_Module:ADXL375 | StrawberryLinux_ADXL375_Module:ADXL375
24 | 1 | U5 | TLP241B | Relay_SolidState:TLP222A | Package_DIP:DIP-4_W7.62mm | https://toshiba.semicon-storage.com/info/docget.jsp?did=17036&prodName=TLP222A
25 | 1 | U6 | ABX00012 | ABX00012:ABX00012 | ABX00012:ARDUINO_ABX00012 |  |  |  | Arduino |  |  |  |  | 5 | Manufacturer Recommendations
26 | 2 | U7, U8 | MB85RS2MT | Memory_NVRAM:MB85RS2MT | Package_DIP:DIP-8_W7.62mm | http://www.fujitsu.com/downloads/MICRO/fsa/pdf/products/memory/fram/MB85RS16-DS501-00014-6v0-E.pdf
27 | 1 | Y1 | 8MHz | Device:Crystal | Crystal:Crystal_SMD_HC49-SD | ~

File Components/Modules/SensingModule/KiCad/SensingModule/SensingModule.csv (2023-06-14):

Source: | /Users/waiwai/Projects/H-58-Avionics/Projects/KiCad/Modules/SensingModule/SensingModule.kicad_sch
Date: | 2023 June 13, Tuesday 16:02:48
Tool: | Eeschema 7.0.1-0
Generator: | /Applications/KiCad/KiCad.app/Contents/SharedSupport/plugins/bom_csv_grouped_by_value.py
Component Count: | 39
Collated Components:
Item | Qty | Reference(s) | Value | LibPart | Footprint | Datasheet | DNP | MANUFACTURER | MAXIMUM_PACKAGE_HEIGHT | PARTREV | SNAPEDA_PN | STANDARD
1 | 2 | C1, C2 | 0.1uF | Device:C | Capacitor_SMD:C_0603_1608Metric_Pad1.08x0.95mm_HandSolder | ~
2 | 1 | C3 | 47uF | Device:C_Polarized | Capacitor_SMD:CP_Elec_6.3x5.9 | ~
3 | 2 | D1, D2 | BLUE | Device:LED | LED_SMD:LED_0603_1608Metric_Pad1.05x0.95mm_HandSolder | ~
4 | 2 | D3, D4 | RED | Device:LED | LED_SMD:LED_0603_1608Metric_Pad1.05x0.95mm_HandSolder | ~
5 | 2 | D5, D6 | GREEN | Device:LED | LED_SMD:LED_0603_1608Metric_Pad1.05x0.95mm_HandSolder | ~
6 | 1 | F1 | Polyfuse | Device:Polyfuse | Fuse:Fuse_1206_3216Metric_Pad1.42x1.75mm_HandSolder | ~
7 | 1 | J1 | Conn_01x08 | Connector_Generic:Conn_01x08 | Hirose_Connector:Hirose_DF11B-8DP-2DS | ~
8 | 1 | J2 | Conn_01x02_Pin | Connector:Conn_01x02_Pin | Hirose_Connector:Hirose_DF1B | ~
9 | 1 | J4 | Micro_SD_Card_Det_Hirose_DM3AT | Connector:Micro_SD_Card_Det_Hirose_DM3AT | Connector_Card:microSD_HC_Hirose_DM3AT-SF-PEJM5 | https://www.hirose.com/product/en/download_file/key_name/DM3/category/Catalog/doc_file_id/49662/?item_id=195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
10 | 2 | R1, R3 | 100R | Device:R | Resistor_SMD:R_0805_2012Metric_Pad1.20x1.40mm_HandSolder | ~
11 | 3 | R2, R6, R8 | 120R | Device:R | Resistor_SMD:R_0603_1608Metric_Pad0.98x0.95mm_HandSolder | ~
12 | 3 | R4, R5, R9 | 10kR | Device:R | Resistor_SMD:R_0805_2012Metric_Pad1.20x1.40mm_HandSolder | ~
13 | 1 | R7 | 2kR | Device:R | Resistor_SMD:R_0603_1608Metric_Pad0.98x0.95mm_HandSolder | ~
14 | 3 | R10, R11, R15 | 300R | Device:R | Resistor_SMD:R_0603_1608Metric_Pad0.98x0.95mm_HandSolder | ~
15 | 3 | R12, R13, R14 | 4.7kR | Device:R | Resistor_SMD:R_0603_1608Metric_Pad0.98x0.95mm_HandSolder | ~
16 | 1 | SW1 | SW_DIP_x02 | Switch:SW_DIP_x02 | Button_Switch_THT:SW_DIP_SPSTx02_Piano_10.8x6.64mm_W7.62mm_P2.54mm | ~
17 | 3 | TP1, TP2, TP3 | TestPoint | Connector:TestPoint | Connector_Pin:Pin_D1.0mm_L10.0mm | ~
18 | 1 | U1 | MCP2562-E-P | Interface_CAN_LIN:MCP2562-E-P | Package_DIP:DIP-8_W7.62mm | http://ww1.microchip.com/downloads/en/DeviceDoc/25167A.pdf
19 | 1 | U2 | BME280 | Akizuki_BME280_Module:BME280 | Akizuki_BME280_Module:BME280
20 | 1 | U3 | BNO055 | Akizuki_BNO055_Module:BNO055 | Akizuki_BNO055_Module:BNO055
21 | 1 | U4 | TLP241B | Relay_SolidState:TLP222A | Package_DIP:DIP-4_W7.62mm | https://toshiba.semicon-storage.com/info/docget.jsp?did=17036&prodName=TLP222A
22 | 1 | U5 | NUCLEO-F303K8 | NUCLEO-F303K8:NUCLEO-F303K8 | NUCLEO-F303K8:MODULE_NUCLEO-F303K8 |  |  | STMicroelectronics | N/A | 5 | NUCLEO-F303K8 | Manufacturer Recommendations
23 | 2 | U6, U7 | MB85RS2MT | Memory_NVRAM:MB85RS2MT | Package_DIP:DIP-8_W7.62mm | http://www.fujitsu.com/downloads/MICRO/fsa/pdf/products/memory/fram/MB85RS16-DS501-00014-6v0-E.pdf

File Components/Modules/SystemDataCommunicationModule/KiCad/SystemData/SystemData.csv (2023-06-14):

Source: | /Users/waiwai/Projects/H-58-Avionics/Projects/KiCad/Modules/CommunicationModule/SystemData/SystemData.kicad_sch
Date: | 2023 June 13, Tuesday 16:19:46
Tool: | Eeschema 7.0.1-0
Generator: | /Applications/KiCad/KiCad.app/Contents/SharedSupport/plugins/bom_csv_grouped_by_value.py
Component Count: | 33
Collated Components:
Item | Qty | Reference(s) | Value | LibPart | Footprint | Datasheet | DNP | DESCRIPTION | MANUFACTURER | MPN | OC_FARNELL | OC_NEWARK | PACKAGE | PARTREV | STANDARD | SUPPLIER | Sim.Device | Sim.Pins
1 | 2 | C1, C8 | 15pF | Device:C | Capacitor_SMD:C_0603_1608Metric_Pad1.08x0.95mm_HandSolder | ~
2 | 4 | C2, C4, C5, C7 | 0.1uF | Device:C | Capacitor_SMD:C_0603_1608Metric_Pad1.08x0.95mm_HandSolder | ~
3 | 1 | C3 | 10uF | Device:C | Capacitor_SMD:C_0603_1608Metric_Pad1.08x0.95mm_HandSolder | ~
4 | 1 | C6 | 47uF | Device:C_Polarized | Capacitor_SMD:CP_Elec_6.3x5.9 | ~
5 | 1 | D1 | RED | Device:LED | LED_SMD:LED_0603_1608Metric_Pad1.05x0.95mm_HandSolder | ~
6 | 1 | D2 | 1N4007 | Diode:1N4007 | Diode_SMD:D_SOD-123F | http://www.vishay.com/docs/88503/1n4001.pdf |  |  |  |  |  |  |  |  |  |  | D | 1=K 2=A
7 | 4 | D3, D4, D5, D6 | BLUE | Device:LED | LED_SMD:LED_0603_1608Metric_Pad1.05x0.95mm_HandSolder | ~
8 | 1 | D7 | GREEN | Device:LED | LED_SMD:LED_0603_1608Metric_Pad1.05x0.95mm_HandSolder | ~
9 | 1 | J1 | Conn_01x08 | Connector_Generic:Conn_01x08 | Hirose_Connector:Hirose_DF11B-8DP-2DS | ~
10 | 1 | R1 | 120R | Device:R | Resistor_SMD:R_0603_1608Metric_Pad0.98x0.95mm_HandSolder | ~
11 | 1 | R2 | 620R | Device:R | Resistor_SMD:R_0603_1608Metric_Pad0.98x0.95mm_HandSolder | ~
12 | 1 | R3 | 10kR | Device:R | Resistor_SMD:R_0805_2012Metric_Pad1.20x1.40mm_HandSolder | ~
13 | 4 | R4, R5, R6, R7 | 100R | Device:R | Resistor_SMD:R_0805_2012Metric_Pad1.20x1.40mm_HandSolder | ~
14 | 1 | R8 | 300R | Device:R | Resistor_SMD:R_0603_1608Metric_Pad0.98x0.95mm_HandSolder | ~
15 | 1 | SW1 | SW_DIP_x02 | Switch:SW_DIP_x02 | Button_Switch_THT:SW_DIP_SPSTx02_Piano_10.8x6.64mm_W7.62mm_P2.54mm | ~
16 | 2 | TP1, TP2 | TestPoint | Connector:TestPoint | Connector_Pin:Pin_D1.0mm_L10.0mm | ~
17 | 1 | U1 | MCP2562-E-P | Interface_CAN_LIN:MCP2562-E-P | Package_DIP:DIP-8_W7.62mm | http://ww1.microchip.com/downloads/en/DeviceDoc/25167A.pdf
18 | 1 | U2 | MCP2515-I/P | MCP2515-I_P:MCP2515-I{slash}P | Package_DIP:DIP-18_W7.62mm |  |  | CAN CONTRL |  | MCP2515-I/P | 1439391 | 61K2945 | PDIP-18 |  |  | MICROCHIP
19 | 1 | U3 | NJM7805SDL1 | Regulator_Linear:L7805 | Package_TO_SOT_SMD:TO-252-2 | http://www.st.com/content/ccc/resource/technical/document/datasheet/41/4f/b3/b0/12/d4/47/88/CD00000444.pdf/files/CD00000444.pdf/jcr:content/translations/en.CD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
20 | 1 | U4 | ABX00012 | ABX00012:ABX00012 | ABX00012:ARDUINO_ABX00012 |  |  |  | Arduino |  |  |  |  | 5 | Manufacturer Recommendations
21 | 1 | U5 | ASX00017 | ArduinoMkrGpsShield:Arduino_MKR_GPS_Shield | ArduinoMkrGpsShield:Arduino MKR GPS Shield
22 | 1 | Y1 | 8MHz | Device:Crystal | Crystal:Crystal_SMD_HC49-SD | ~

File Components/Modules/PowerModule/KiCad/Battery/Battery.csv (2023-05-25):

Source: | /Users/waiwai/Projects/H-58-Avionics/Projects/KiCad/Modules/PowerModule/Battery/Battery.kicad_sch
Date: | 2023 May 22, Monday 14:22:17
Tool: | Eeschema 7.0.1-0
Generator: | /Applications/KiCad/KiCad.app/Contents/SharedSupport/plugins/bom_csv_grouped_by_value.py
Component Count: | 11
Collated Components:
Item | Qty | Reference(s) | Value | LibPart | Footprint | Datasheet | DNP
1 | 10 | BT1, BT2, BT3, BT4, BT5, BT6, BT7, BT8, BT9, BT10 | Battery_Cell | Device:Battery_Cell | KiCad:CR123APC | ~
2 | 1 | J1 | Conn_01x02_Socket | Connector:Conn_01x02_Pin | CONNECTOR:CONNECTOR_2-STRAIGHT | ~

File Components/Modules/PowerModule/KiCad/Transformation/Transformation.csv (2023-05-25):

Source: | /Users/waiwai/Projects/H-58-Avionics/Projects/KiCad/Modules/PowerModule/Transformation/Transformation.kicad_sch
Date: | 2023 May 23, Tuesday 14:07:54
Tool: | Eeschema 7.0.1-0
Generator: | /Applications/KiCad/KiCad.app/Contents/SharedSupport/plugins/bom_csv_grouped_by_value.py
Component Count: | 46
Collated Components:
Item | Qty | Reference(s) | Value | LibPart | Footprint | Datasheet | DNP | MANUFACTURER_PART_NUMBER | Sim.Device | Sim.Pins | VENDOR
1 | 9 | C1, C7, C8, C10, C11, C12, C13, C14, C15 | 270μF | Device:C | Capacitor_THT:CP_Radial_D10.0mm_P3.50mm | ~
2 | 3 | C2, C6, C9 | 0.1μF | Device:C | Capacitor_SMD:C_0603_1608Metric_Pad1.08x0.95mm_HandSolder | ~
3 | 3 | C3, C4, C5 | 10μF | Device:C | Capacitor_SMD:C_0603_1608Metric_Pad1.08x0.95mm_HandSolder | ~
4 | 9 | D1, D2, D3, D4, D5, D6, D7, D8, D9 | 1N4007 | Diode:1N4007 | Diode_SMD:D_SOD-123F | http://www.vishay.com/docs/88503/1n4001.pdf |  |  | D | 1=K 2=A
5 | 1 | D10 | RED | Device:LED | LED_SMD:LED_0603_1608Metric_Pad1.05x0.95mm_HandSolder | ~
6 | 4 | J1, J2, J3, J4 | Conn_01x02_Pin | Connector:Conn_01x02_Pin | Hirose_Connector:Hirose_DF1B | ~
7 | 3 | Q1, Q2, Q3 | TJ8S06M3L | Transistor_FET:QM6015D | Package_TO_SOT_SMD:TO-252-2 | http://www.jaolen.com/images/pdf/QM6015D.pdf
8 | 1 | R1 | 120kΩ | Device:R | Resistor_SMD:R_0603_1608Metric_Pad0.98x0.95mm_HandSolder | ~
9 | 1 | R2 | 10kΩ | Device:R | Resistor_SMD:R_0603_1608Metric_Pad0.98x0.95mm_HandSolder | ~
10 | 1 | R3 | 2kΩ | Device:R | Resistor_SMD:R_0603_1608Metric_Pad0.98x0.95mm_HandSolder | ~
11 | 1 | R4 | 68kΩ | Device:R | Resistor_SMD:R_0603_1608Metric_Pad0.98x0.95mm_HandSolder | ~
12 | 1 | SW1 | SW_SPDT | Switch:SW_SPDT | 2MS1T1B4M7QES:2MS1T1B4M7QES | ~
13 | 5 | TP1, TP2, TP3, TP4, TP5 | TestPoint | Connector:TestPoint | Connector_Pin:Pin_D1.0mm_L10.0mm | ~
14 | 3 | U1, U2, U3 | NJM7812SDL1 | Regulator_Linear:L7812 | Package_TO_SOT_SMD:TO-252-2 | http://www.st.com/content/ccc/resource/technical/document/datasheet/41/4f/b3/b0/12/d4/47/88/CD00000444.pdf/files/CD00000444.pdf/jcr:content/translations/en.CD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
15 | 1 | U4 | LTC4416EMS#PBF | LTC4416EMS_PBF:LTC4416EMS#PBF | Package_SO:MSOP-10-1EP_3x3mm_P0.5mm_EP1.73x1.98mm |  |  | ltc4416ims1 |  |  | Linear Technology

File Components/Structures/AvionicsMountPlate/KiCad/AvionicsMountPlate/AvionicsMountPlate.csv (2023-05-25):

Source: | /Users/waiwai/Projects/H-58-Avionics/Projects/KiCad/Structures/AvionicsMountPlate/AvionicsMountPlate.kicad_sch
Date: | 2023 May 22, Monday 14:21:49
Tool: | Eeschema 7.0.1-0
Generator: | /Applications/KiCad/KiCad.app/Contents/SharedSupport/plugins/bom_csv_grouped_by_value.py
Component Count: | 0
Collated Components:
Item | Qty | Reference(s) | Value | LibPart | Footprint | Datasheet | DNP

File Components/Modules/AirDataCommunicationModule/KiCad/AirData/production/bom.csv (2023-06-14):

Designator | Footprint | Quantity | Value | LCSC Part #
C1, C7 | 0603 | 2 | 15pF
C2 | 0603 | 1 | 10uF
C3, C4, C5, C6 | 0603 | 4 | 0.1uF
C8 | CP_Elec_6.3x5.9 | 1 | 47uF
D1 | 0603 | 1 | RED
D2, D3, D5, D6 | 0603 | 4 | BLUE
D4 | D_SOD-123F | 1 | 1N4007
J1 | Hirose_DF11B-8DP-2DS | 1 | Conn_01x08
R1 | 0603 | 1 | 120R
R2 | 0603 | 1 | 620R
R3 | 0805 | 1 | 10kR
R4, R5, R6, R7 | 0805 | 4 | 100R
SW1 | SW_DIP_SPSTx02_Piano_10.8x6.64mm_W7.62mm_P2.54mm | 1 | SW_DIP_x02
TP1, TP2 | Pin_D1.0mm_L10.0mm | 2 | TestPoint
U1 | DIP-8_W7.62mm | 1 | MCP2562-E-P
U2 | DIP-18_W7.62mm | 1 | MCP2515-I/P | MCP2515-I/P
U3 | TO-252-2 | 1 | NJM7805SDL1
U4 | ARDUINO_ABX00012 | 1 | ABX00012
Y1 | Crystal_SMD_HC49-SD | 1 | 8MHz

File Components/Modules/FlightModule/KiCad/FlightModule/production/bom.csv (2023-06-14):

Designator | Footprint | Quantity | Value | LCSC Part #
BZ1 | Buzzer_12x9.5RM7.6 | 1 | Buzzer
C1, C2, C4 | 0603 | 3 | 0.1uF
C3 | CP_Elec_6.3x5.9 | 1 | 47uF
D1, D2 | 0603 | 2 | BLUE
D10, D5 | 0603 | 2 | RED
D11, D12, D13, D14, D3, D4 | 0603 | 6 | GREEN
D6, D7 | D_SOD-123F | 2 | 1N4007
J1 | Hirose_DF11B-8DP-2DS | 1 | Conn_01x08
J2, J3, J4, J5, J6 | Hirose_DF1B | 5 | Conn_01x02_Pin
Q1, Q2 | SC-59_Handsoldering | 2 | Q_NPN_BEC
R1, R11, R12, R14, R15 | 0603 | 5 | 120R
R10, R17, R20 | 0603 | 3 | 2kR
R13, R18, R19, R21, R22 | 0603 | 5 | 300R
R16, R26, R27, R30, R31 | 0603 | 5 | 4.7kR
R2, R7 | 0603 | 2 | 820R
R23, R24 | 0805 | 2 | 10kR
R25 | 0603 | 1 | 1kR
R3 | 0603 | 1 | 4.3kR
R4 | 0603 | 1 | 5.6kR
R5, R6 | 0805 | 2 | 100R
R8 | 0603 | 1 | 750R
R9 | 0603 | 1 | 3kR
SW1 | SW_DIP_SPSTx02_Piano_10.8x6.64mm_W7.62mm_P2.54mm | 1 | SW_DIP_x02
TP1, TP2, TP3, TP4, TP5, TP6 | Pin_D1.0mm_L10.0mm | 6 | TestPoint
U1 | DIP-8_W7.62mm | 1 | MCP2562-E-P
U2 | MODULE_NUCLEO-F303K8 | 1 | NUCLEO-F303K8
U3, U4 | DIP-4_W7.62mm | 2 | TLP241B
U5 | DIP-8_W7.62mm | 1 | MB85RS2MT

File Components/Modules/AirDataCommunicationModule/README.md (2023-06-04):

# 通信モジュール

AirData
SystemData

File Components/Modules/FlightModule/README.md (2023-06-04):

# フライトモジュール

FlightModule

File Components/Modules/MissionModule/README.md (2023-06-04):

# ミッションモジュール

MissionModule

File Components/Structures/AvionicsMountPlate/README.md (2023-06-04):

# 計器マウントプレート

AvionicsMountPlate

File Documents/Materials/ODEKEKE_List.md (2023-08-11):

# 渡航に必要なものリスト

## 2023年度 能代宇宙イベント打ち上げ実験用

渡航に必要なものをここに記す

### 実際に用意したもの
| 名称 | 【企業名】 | (個数/在庫=所持している分) | 参考リンク |
| ---- | --- | --- | --- |

---
### E0 風向風速計ケース(1217W×500D×43H)

- [ ] 風向風速計セット
  - [ ] 風速計【Onset社】(x1) [Z-Storage](https://drive.google.com/drive/folders/1pr7K7Y3kVD4iESg3JlFsGhEIkhMSgURr)
  - [ ] 風向計【Onset社】(x1) [Z-Storage](https://drive.google.com/drive/folders/1pr7K7Y3kVD4iESg3JlFsGhEIkhMSgURr)
  - [ ] 雨量計【Onset社】(x1) [Z-Storage](https://drive.google.com/drive/folders/1pr7K7Y3kVD4iESg3JlFsGhEIkhMSgURr)
  - [ ] 圧力計【Onset社】(x1) [Z-Storage](https://drive.google.com/drive/folders/1pr7K7Y3kVD4iESg3JlFsGhEIkhMSgURr)
  - [ ] 温度計【Onset社】(x1) [Z-Storage](https://drive.google.com/drive/folders/1pr7K7Y3kVD4iESg3JlFsGhEIkhMSgURr)
  - [ ] データロガー【Onset社】(x1) [Z-Storage](https://drive.google.com/drive/folders/1pr7K7Y3kVD4iESg3JlFsGhEIkhMSgURr)
  - [ ] データロガー専用充電器【Onset社】(x1) [Z-Storage](https://drive.google.com/drive/folders/1pr7K7Y3kVD4iESg3JlFsGhEIkhMSgURr)
  - [ ] ソーラーラジエーションシールド【Onset社】(x1) [Z-Storage](https://drive.google.com/drive/folders/1pr7K7Y3kVD4iESg3JlFsGhEIkhMSgURr)
  - [ ] アルミ四角柱【Onset社】(x1) [Z-Storage](https://drive.google.com/drive/folders/1pr7K7Y3kVD4iESg3JlFsGhEIkhMSgURr)
  - [ ] 支柱本体【Onset社】(x1) [Z-Storage](https://drive.google.com/drive/folders/1pr7K7Y3kVD4iESg3JlFsGhEIkhMSgURr)
  - [ ] 各種取り付けねじ【Onset社】(x1) [Z-Storage](https://drive.google.com/drive/folders/1pr7K7Y3kVD4iESg3JlFsGhEIkhMSgURr)
  - [ ] 各種取り付け工具
    - [ ] レンチ
    - [ ] タイラップ等

- [ ]　その他類
  - [ ] 三脚「安定感マシマシ」【わからん】(x1) [わからん]()
  - [ ] 三脚「チビヒョロ」【わからん】(x1) [わからん]()

- [ ] RaspberryPi関係
  - [ ] RasPad【】() [ | ]()
  - [ ] 赤外線カメラモジュールV2【RSコンポーネンツ株式会社(OKdo)】(x1) [RSコンポーネンツ株式会社(OKdo) | 913-2673](https://jp.rs-online.com/web/p/raspberry-pi-cameras/9132673)
  - [ ] カメラモジュールV2【RSコンポーネンツ株式会社(OKdo)】(x1) [RSコンポーネンツ株式会社(OKdo) | 913-2664](https://jp.rs-online.com/web/p/raspberry-pi-cameras/9132664)
  - [ ] MicroHDMI変換コネクタ【わからん】(x1) [ | ]()
  - [ ] CtoC USBケーブル【】() [ | ]()
  - [ ] 中原キーボード【】() [ | ]()
  - [ ] 赤マウス【】() [ | ]()
  - [ ] 

---
### E1 エレキ工具箱(23Wx49Dx29H)

- 1段目
  - [ ] はんだごて【HAKKO】(x2) [HAKKO | FX-600](https://www.hakko.com/japan/products/hakko_fx600.html)
    - [ ] こて先【HAKKO】(x2) [HAKKO | ]()
  - [ ] グルーガン【100均】(x1) [100均]()
  - [ ] 鉛フリーはんだ【わからん】(x1) [わからん]()
  - [ ] 低融点はんだ【わからん】(x1) [わからん]()
  - [ ] はんだ吸い取り線【わからん】(x3) [わからん]()
  - [ ] タイラップ【わからん】(x2) [わからん]()
  - [ ] やすりセット【HOZAN】(x1) [HOZAN | K-155-L]()
  - [ ] ソルダーアシストセット【わからん】(x1) [わからん]()
  - [ ] 接着剤セット【セメダイン】(x1) [セメダイン]()
- 2段目
  - [ ] ワイヤーストリッパー【SKII】(x1) [藤原産業 | DVC-WS102](http://www.fujiwarasangyo-markeweb2.com/DispDetail.do?volumeName=00017&itemID=t000100184313)
  - [ ] ワイヤーストリッパー【HOZAN】(x1) [HOZAN | P-978](https://www.hozan.co.jp/corp/g/g6978/)
  - [ ] 精密圧着ペンチ【エンジニアー】(x1) [エンジニアー | PA-09](https://www.nejisaurus.engineer.jp/product-page/pa-09-%E7%B2%BE%E5%AF%86%E5%9C%A7%E7%9D%80%E3%83%9A%E3%83%B3%E3%83%81-1)
  - [ ] 精密圧着ペンチ【エンジニアー】(x1) [エンジニアー | PA-21](https://www.nejisaurus.engineer.jp/product-page/pa-21-%E7%B2%BE%E5%AF%86%E5%9C%A7%E7%9D%80%E3%83%9A%E3%83%B3%E3%83%81-1)
  - [ ] ニッパー【エンジニアー】(x1) [エンジニアー | NZ-13G ESD](https://www.nejisaurus.engineer.jp/product-page/nz-13g-esd%E3%83%9F%E3%82%AF%E3%83%AD%E3%82%AB%E3%83%83%E3%82%BF%E3%83%BC-1)
  - [ ] 斜ニッパー【HOZAN】(x1) [HOZAN | N-5-125](https://www.hozan.co.jp/corp/g/g6055/)
  - [ ] ラジオペンチ【HOZAN】(x1) [HOZAN]()
  - [ ] ESDチップピンセット【HOZAN】(x1) [HOZAN | P-642-S](https://www.hozan.co.jp/corp/g/g6612/)
  - [ ] ピンセット【goot】(x2) [goot | TS-16](https://www.goot.jp/products/detail/ts_16)
  - [ ] はさみ【わからん】(x1) [わからん]()
  - [ ] 六角レンチ【わからん】(x1) [わからん]()
  - [ ] 布絶縁テープ【わからん】(x1) [わからん]()
  - [ ] マスキングテープ【3M】(x3) [3M | ](https://www.3mcompany.jp/3M/ja_JP/p/d/v000452993/)
  - [ ] 熱収縮チューブφ10【住友重工エファインポリマー株式会社】(x1) [秋月電子通商](https://akizukidenshi.com/catalog/g/gP-08985/)
  - [ ] 熱収縮チューブφ3【住友重工エファインポリマー株式会社】(x1) [秋月電子通商](https://akizukidenshi.com/catalog/g/gP-06789/)
- 3段目
  - [ ] ドリル刃セット【わからん】(x1) [わからん]()
  - [ ] プラスドライバー【わからん】(x2) [わからん]()
  - [ ] ビット変換可能ドライバー【わからん】(x1) [わからん]()
  - [ ] デジタルマルチメーター【Kaise】(x1) [Kaise株式会社 | KU-2602](https://www.kaise.com/j_dmm_ku2602.html)
  - [ ] ペン型デジタルマルチメーター【イチネンTASCO株式会社】(x1) [イチネンTASCO株式会社 | TA452CT](https://www.tascojapan.co.jp/product.php?prc=detail&sid=2901)

---
### E2 ジュラルミンケース(42Wx25Dx325H)

- [ ] マルチクランプ【goot】(x1) [goot | ST-85](https://goot.jp/products/detail/st_85)
- [ ] 作業ヘルパーツイ・サポ【goot】(x1) [goot | ST-95](https://goot.jp/products/detail/st_95)
- [ ] こて台【HAKKO】(x2) [HAKKO | 633-01](https://www.hakko.com/japan/products/hakko_kote_board_feature.html)
  - [ ] こて先クリーナー【HAKKO】(x2) [HAKKO | 599B-01](https://www.hakko.com/japan/products/hakko_kote_board_option.html)
- [ ] キムワイプ【日本製紙クレシア】(x2) [日本製紙クレシア | S-200](https://pro.crecia.co.jp/search/paper_wiper/paper_wiper_boxwiper/url1)
- [ ] アンビリカルケーブル【TSRP】(x1) [Github | UmbilicalCable]()
- [ ] ランチャアタッチメント【TSRP】
  - [ ] くそでかワッシャ【TSRP】(x2) [Github | KusodekaWasher]()
  - [ ] ランチャに線固定するやつ【TSRP】(x2) [Github | LunchernisenkoteisuruYATU]()
  - [ ] 線がぷらぷらしないようにするやつ【TSRP】(x2) [Github | SengapurapurasinaiyounisuruYATU]()
- [ ] 線材
  - [ ] 赤(AWG24)【協和ハーモネット】(x1) [協和ハーモネット | UL1007AWG24 100m RD](https://www.monotaro.com/p/6242/6264/)
  - [ ] 黒(AWG24)【協和ハーモネット】(x1) [協和ハーモネット | UL1007AWG24 100m BK](https://www.monotaro.com/p/6242/6343/)
  - [ ] 黄(AWG24)【協和ハーモネット】(x1) [協和ハーモネット | UL1007AWG24 100m YL](https://www.monotaro.com/p/6242/6289/)
  - [ ] 青(AWG24)【協和ハーモネット】(x1) [協和ハーモネット | UL1007AWG24 100m BL](https://www.monotaro.com/p/6242/6307/)

---
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

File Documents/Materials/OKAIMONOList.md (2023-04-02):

# お買い物リスト

2023年度すぐに買うものリスト。

## 直接買いに行く

- マイコン
  - ~~Nucleo-F303K8 (x5)~~ 3個購入済み
    - [秋月](https://akizukidenshi.com/catalog/g/gM-10172/) (¥2,200)
    - [DigiKey](https://www.digikey.jp/short/vvwbvcq3) ($10.99)
- IC
  - ~~MCP2515 (x3) ... CANコントローラ~~
    - [秋月](https://akizukidenshi.com/catalog/g/gI-12030/) (¥350)
  - ~~MCP2562 (x5) ... CANトランシーバ~~
    - [秋月](https://akizukidenshi.com/catalog/g/gI-14383/) (¥190)
  - ~~TLP241B (x4) ... フォトカプラ~~
    - [秋月](https://akizukidenshi.com/catalog/g/gI-16705/) (¥180)
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

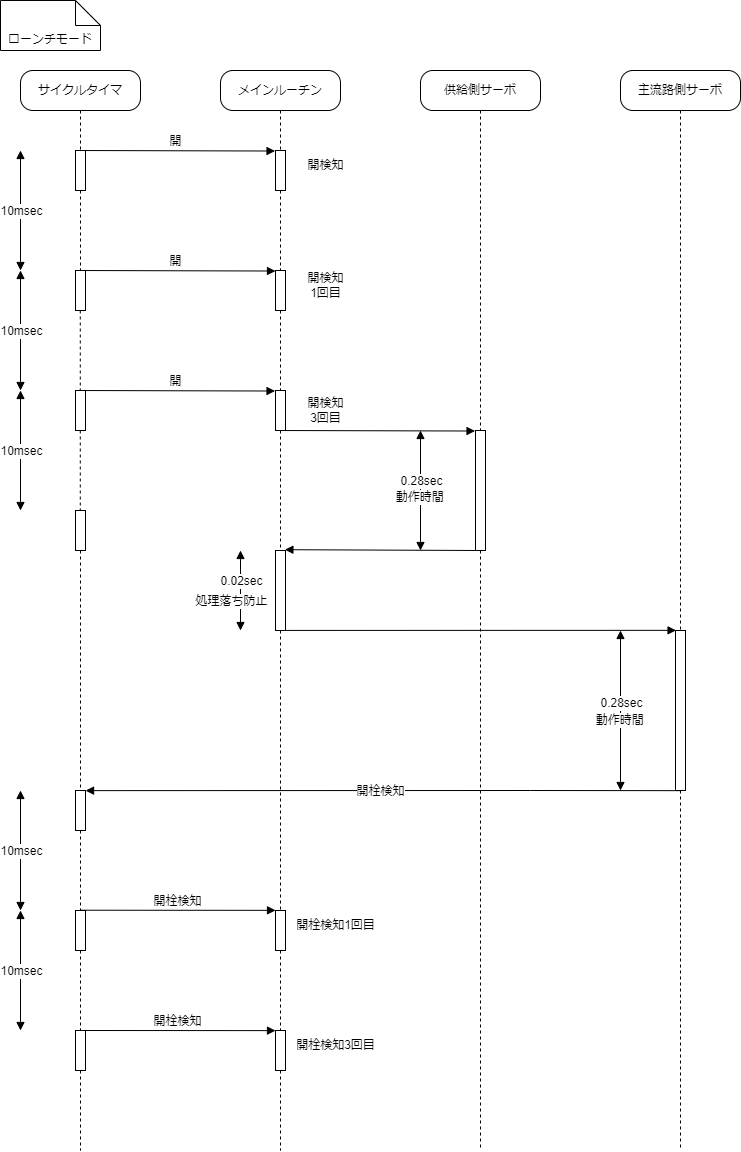
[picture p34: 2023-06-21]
Documents/Materials/images/Logics/ValveControlTimingChart_LaunchMode.png

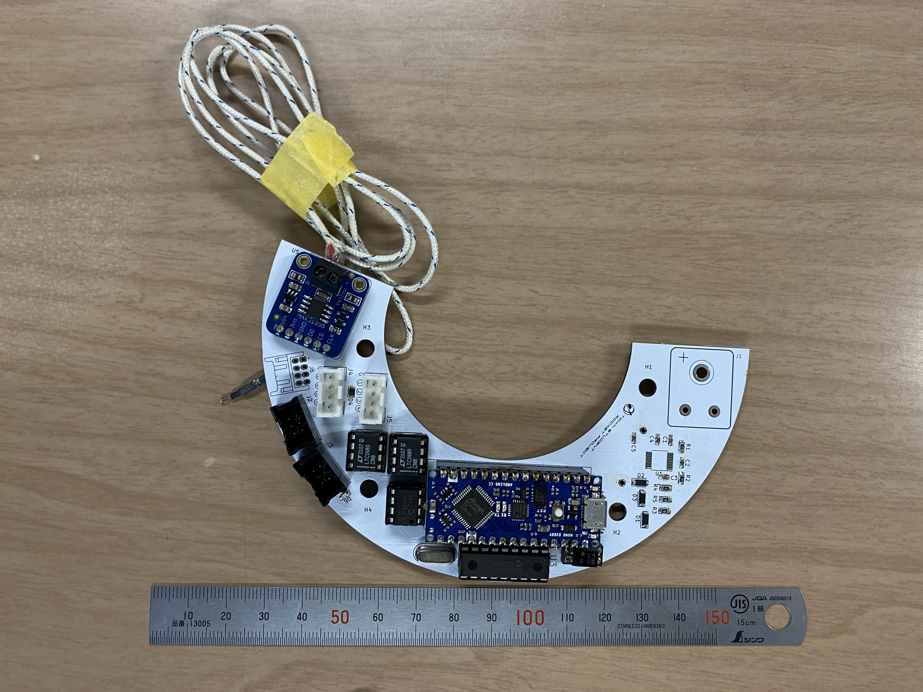
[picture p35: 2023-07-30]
Documents/Materials/Manual/images/parts/boards/CANComunicationDemonstrationModuleBoard.JPG

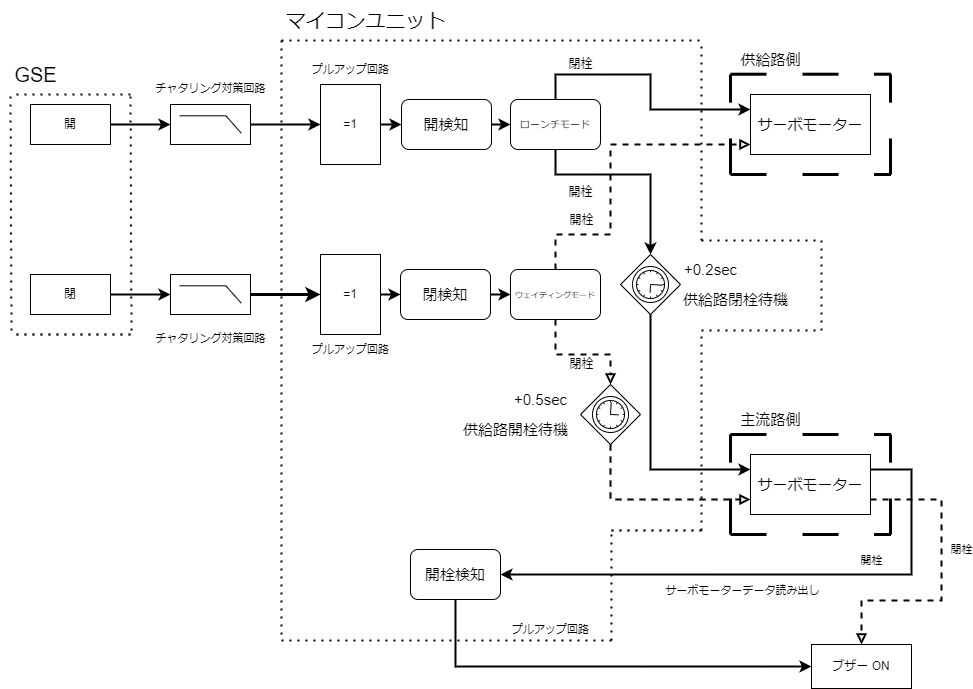
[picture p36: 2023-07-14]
Documents/Materials/images/Logics/ValveControlLogic.png

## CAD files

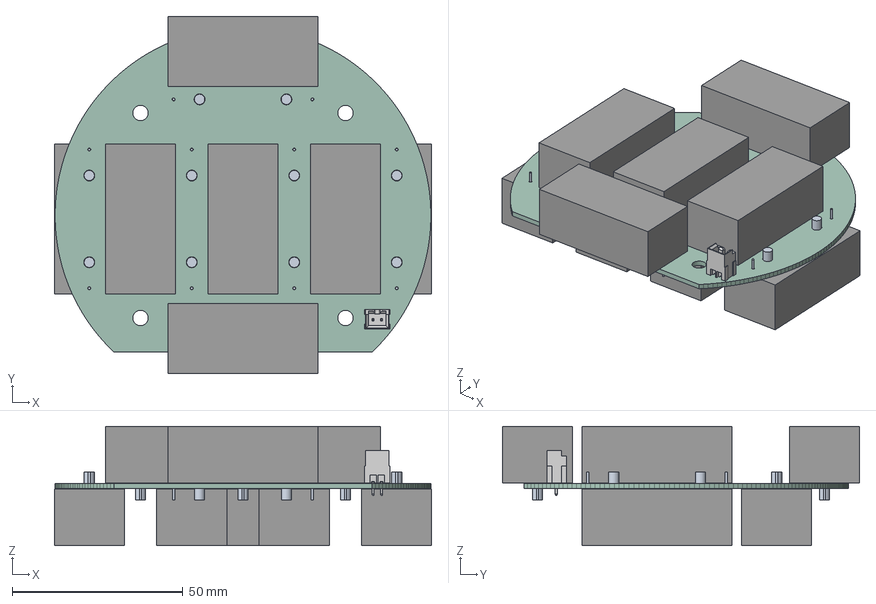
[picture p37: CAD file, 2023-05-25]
Components/Modules/PowerModule/KiCad/Battery/Battery.step
110.5 x 104.5 x 34.9 mm
PCB

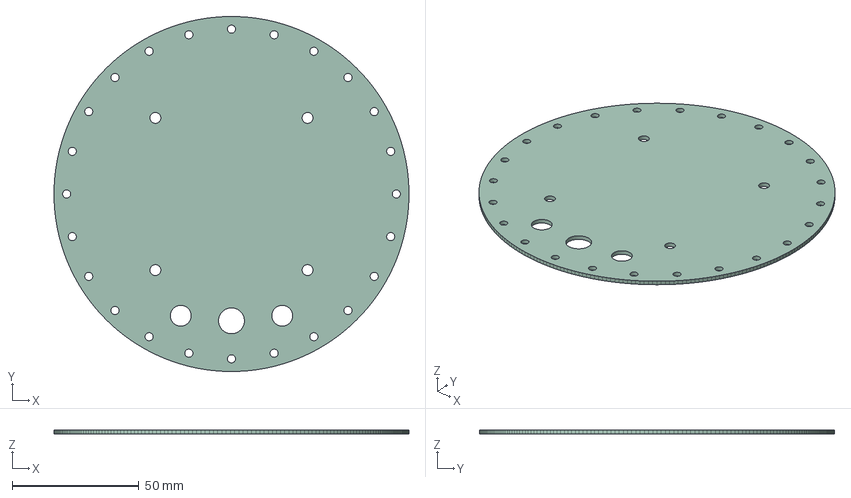
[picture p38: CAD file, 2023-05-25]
Components/Structures/AvionicsMountPlate/KiCad/AvionicsMountPlate/AvionicsMountPlate.step
140.0 x 140.0 x 1.60 mm

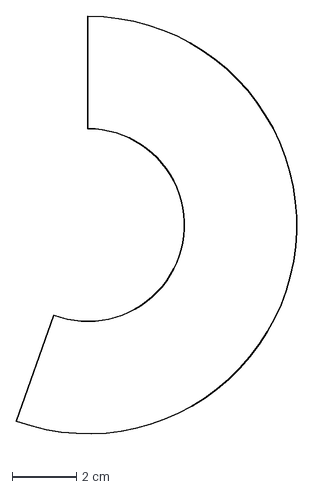
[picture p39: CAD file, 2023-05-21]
Projects/AutoCAD/THRControlModule/THRControlModule_Shape_fai60_200deg.dxf
9.23 x 13.5 cm

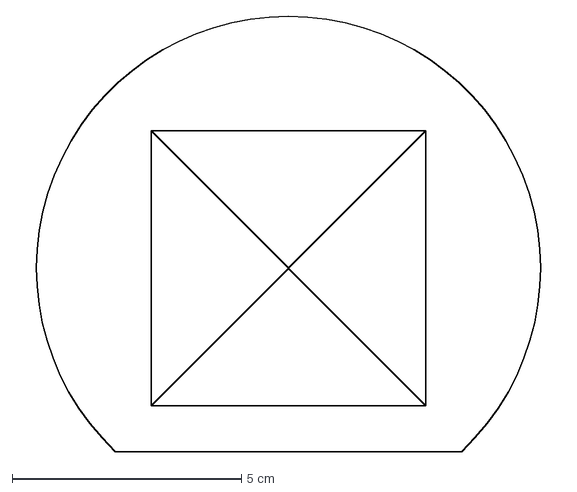
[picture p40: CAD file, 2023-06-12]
Projects/AutoCAD/StandardModule/StandardModuleBoardShape_v2.0.dxf
11.9 x 9.50 cm

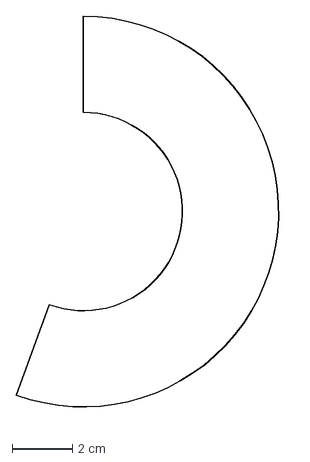
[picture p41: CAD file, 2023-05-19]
Projects/AutoCAD/THRControlModule/THRControlModule_Shape_fai66_200deg.dxf
9.22 x 13.5 cm

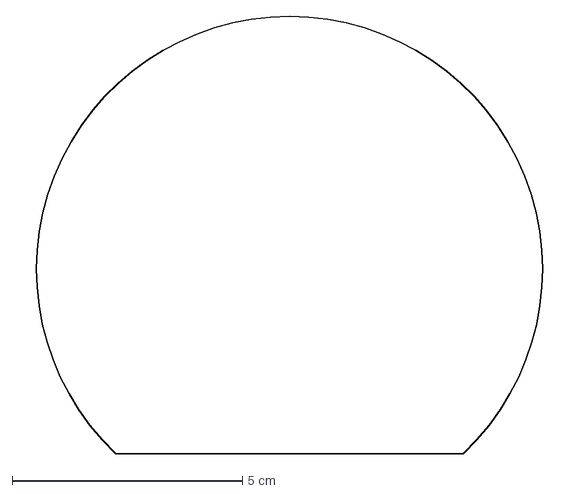
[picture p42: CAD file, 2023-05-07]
Projects/AutoCAD/StandardModule/StandardModuleBoard_Shape.dxf
11.9 x 9.50 cm

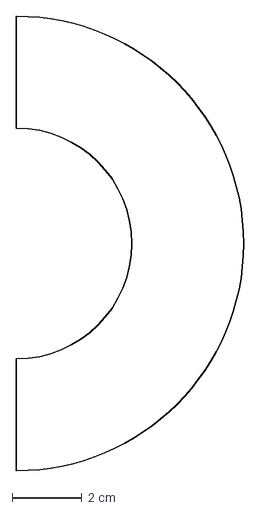
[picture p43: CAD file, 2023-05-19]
Projects/AutoCAD/THRControlModule/THRControlModule_Shape_fai66_120deg.dxf
6.50 x 13.0 cm

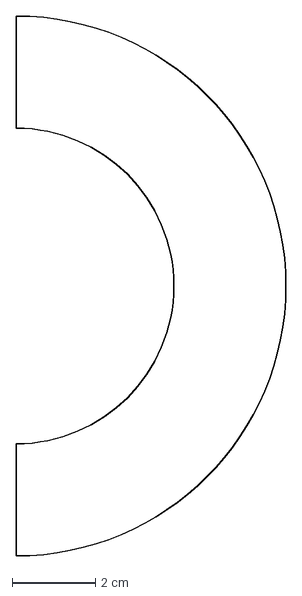
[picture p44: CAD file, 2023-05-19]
Projects/AutoCAD/THRControlModule/THRControlModule_Shape_180deg.dxf
6.50 x 13.0 cm

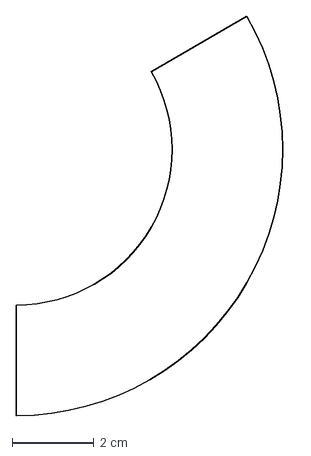
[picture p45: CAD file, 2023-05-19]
Projects/AutoCAD/THRControlModule/THRControlModule_Shape_120deg.dxf
6.79 x 9.75 cm

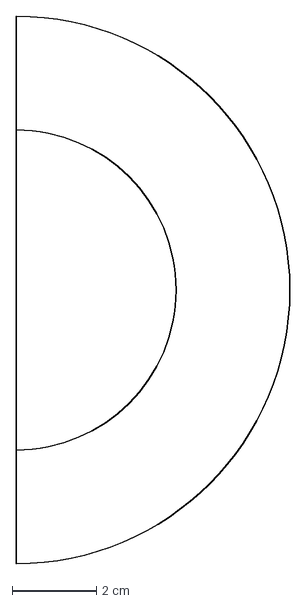
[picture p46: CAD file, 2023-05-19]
Projects/AutoCAD/THRControlModule/THRControlModule_Shape_180deg v1.dxf
6.50 x 13.0 cm

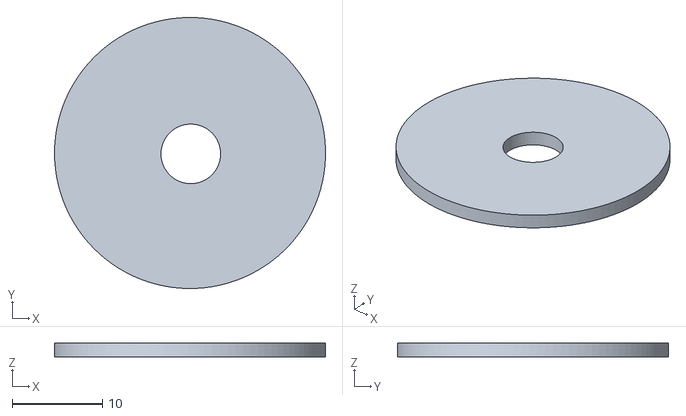
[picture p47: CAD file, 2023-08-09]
Components/Structures/KusodekaWasher/ランチャアタッチメント_2_クソデカワッシャ.stl
30.0 x 30.0 x 1.60

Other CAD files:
Projects/AutoCAD/StandardModule/StandardModuleBoardShape_ver2.0.dwg
Projects/AutoCAD/StandardModule/StandardModuleBoardShapeWithSTM.dwg
Projects/AutoCAD/StandardModule/StandardModuleBoardShapeLegacy.dwg
Projects/AutoCAD/StandardModule/StandardModuleBoardShape.dwg

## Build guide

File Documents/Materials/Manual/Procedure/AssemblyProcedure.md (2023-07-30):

# 組み立て手順書

| 種別 | 所要時間 | 最低人員 |
| --- | --- | --- |
| 通常運用 | 20分 | 1人 |

計器タワーの組み立て手順です。計器チューブ取り付けから機体搭載は[機体搭載手順書](MountingProcedure.md)を参照してください。

## 必要物品

### 部品

写真はこちら -> [部品一覧](../PartsList.md)

- 基板
  - [ ] 1x 電池ボックス基板
  - [ ] 1x 変圧基板
  - [ ] 1x バルブ制御モジュール基板
  - [ ] 1x 計測モジュール基板
  - [ ] 1x フライトモジュール基板
  - [ ] 1x ミッションモジュール基板
  - [ ] 1x エアデータ通信モジュール基板
  - [ ] 1x システムデータ通信モジュール基板
  - [ ] 1x カメラモジュール基板
- 構造
  - [ ] 1x 計器ベースプレート
  - [ ] 4x M4x20mm スペーサー
  - [ ] 28x M4x10mm スペーサー
  - [ ] 24x M4 ワッシャー
  - [ ] 4x M4 ナット
  - [ ] 6x アンテナ固定用タイラップ
- 配線
  - [ ] 1x VREF配線
  - [ ] 1x SN3配線
  - [ ] 1x CAMERA配線

### 工具

- [ ] M3,M4 スパナ

## 手順

### 0. 計器ベースプレートの準備

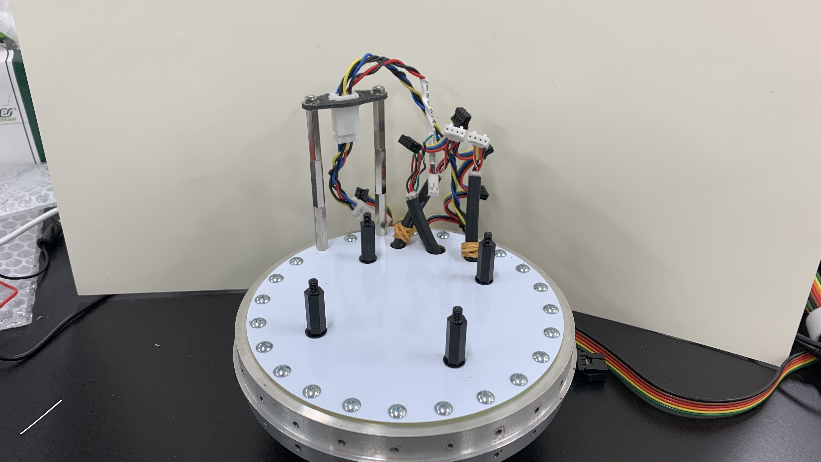
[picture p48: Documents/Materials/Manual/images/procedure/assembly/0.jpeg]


> 1x 計器ベースプレート

運用時は写真の状態から解体することはありません。

### 1. 電池ボックス基板取り付け

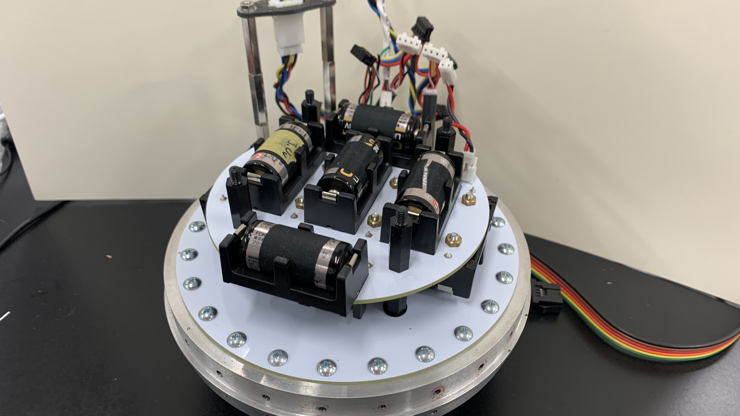
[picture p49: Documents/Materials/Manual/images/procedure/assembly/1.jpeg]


> 1x 電池ボックス基板
> 4x M4x20mm スペーサー

基板の裏表に注意してください。コネクタのある面が表です。

スペーサーの取り付けトルクは「手締めで限界まで+スパナで30°」を目安にしてください。

### 2. 変圧基板取り付け

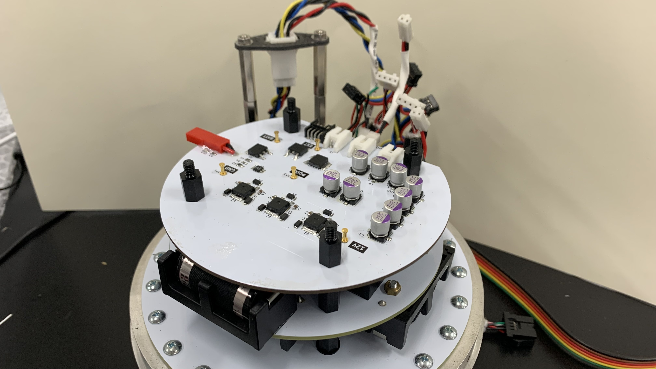
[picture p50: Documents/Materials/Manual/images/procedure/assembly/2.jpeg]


> 1x 変圧基板
> 4x M4x10mm スペーサー
>
> ### 3. バルブ制御モジュール基板取り付け

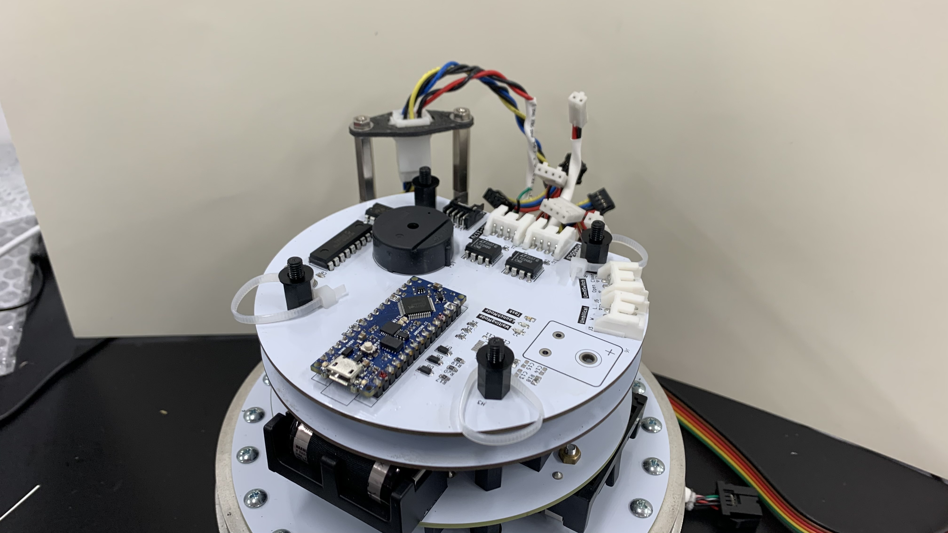
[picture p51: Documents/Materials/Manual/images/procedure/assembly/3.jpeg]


> 1x バルブ制御モジュール基板
> 4x M4x10mm スペーサー
> 3x アンテナ固定用タイラップ
> 4x M4 ワッシャー

アンテナ固定用タイラップを忘れずに。

### 4. 計測モジュール基板取り付け

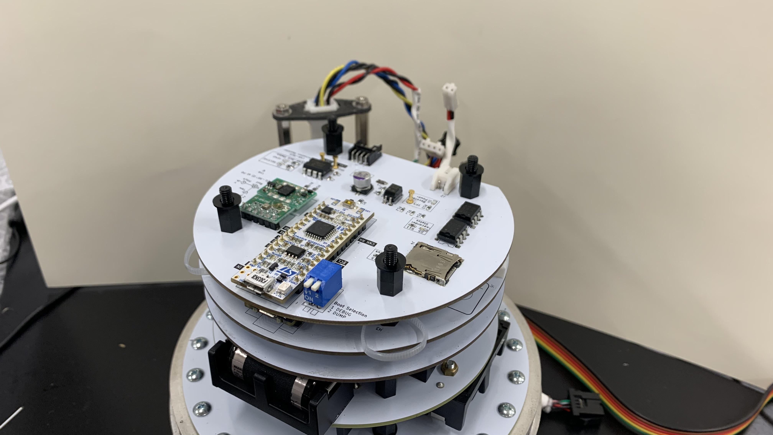
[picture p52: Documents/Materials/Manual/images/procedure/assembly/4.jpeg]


> 1x 計測モジュール基板
> 4x M4x10mm スペーサー
> 4x M4 ワッシャー

### 5. フライトモジュール基板取り付け

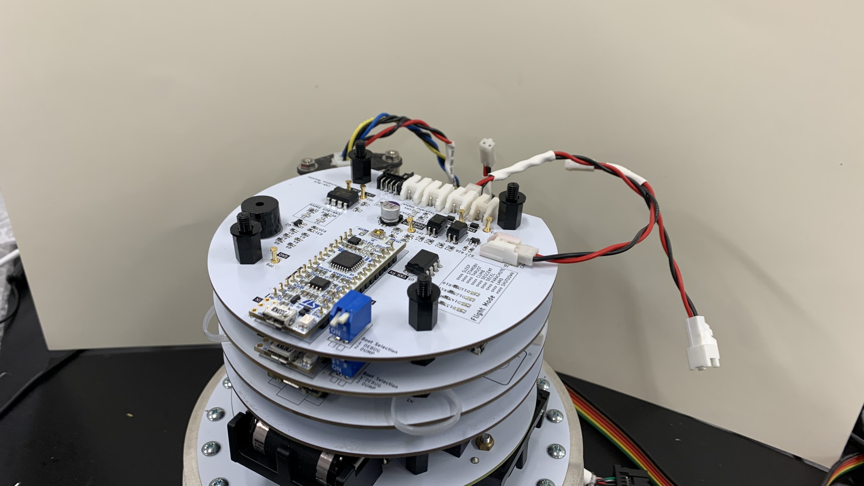
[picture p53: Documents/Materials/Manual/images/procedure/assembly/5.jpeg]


> 1x フライトモジュール基板
> 4x M4x10mm スペーサー
> 4x M4 ワッシャー

### 6. ミッションモジュール基板取り付け

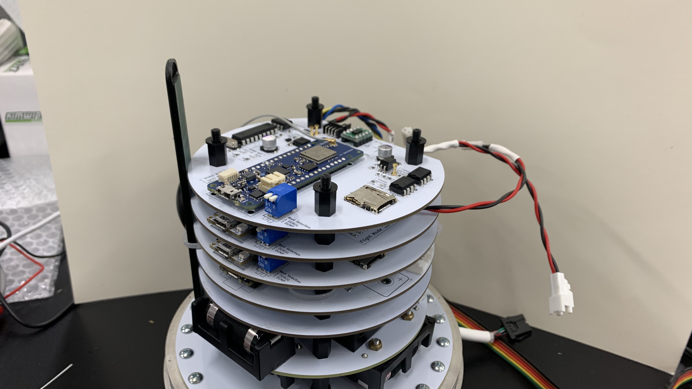
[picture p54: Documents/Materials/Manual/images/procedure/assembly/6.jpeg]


> 1x ミッションモジュール基板
> 4x M4x10mm スペーサー
> 4x M4 ワッシャー

### 7. エアデータ通信モジュール基板取り付け

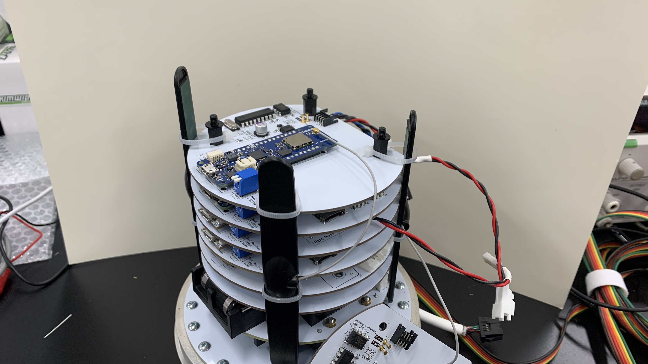
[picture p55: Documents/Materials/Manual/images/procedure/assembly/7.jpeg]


> 1x エアデータ通信モジュール基板
> 4x M4x10mm スペーサー
> 3x アンテナ固定用タイラップ
> 4x M4 ワッシャー

アンテナ固定用タイラップを忘れずに。

次に取り付けるシステムデータ通信モジュールのアンテナもこのタイミングで固定しましょう。

### 8. システムデータ通信モジュール基板取り付け


TODO: 写真追加

> 1x システムデータ通信モジュール基板
> 4x M4x10mm スペーサー
> 4x M4 ワッシャー

### 9. カメラモジュール基板取り付け

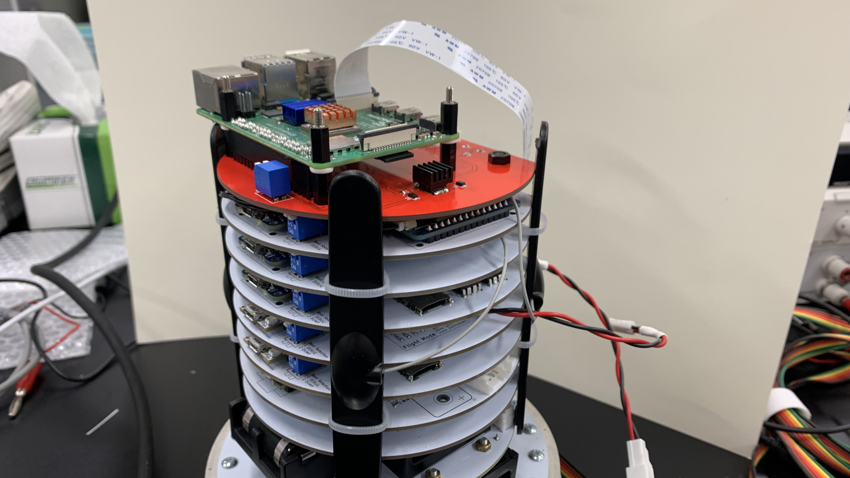
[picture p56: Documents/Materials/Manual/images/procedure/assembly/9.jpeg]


> 1x カメラモジュール基板
> 4x M4 ナット

### 10. 配線接続

#### 10.1. データバス接続

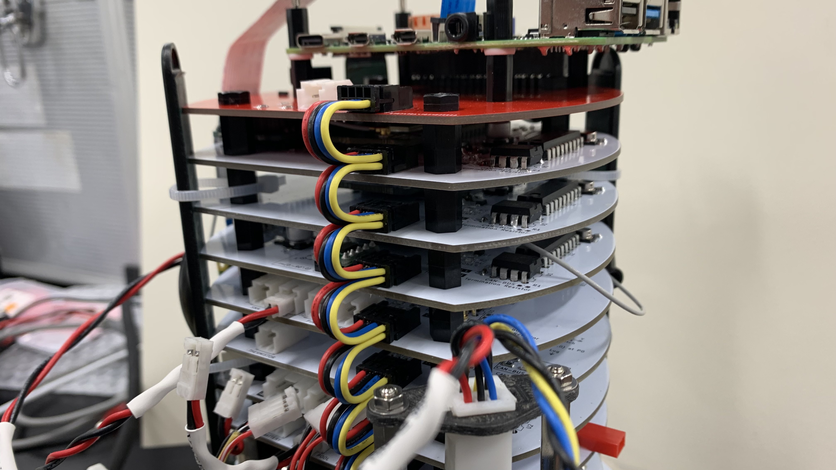
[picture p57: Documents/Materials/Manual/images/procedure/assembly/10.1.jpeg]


#### 10.2. 変圧基板の配線

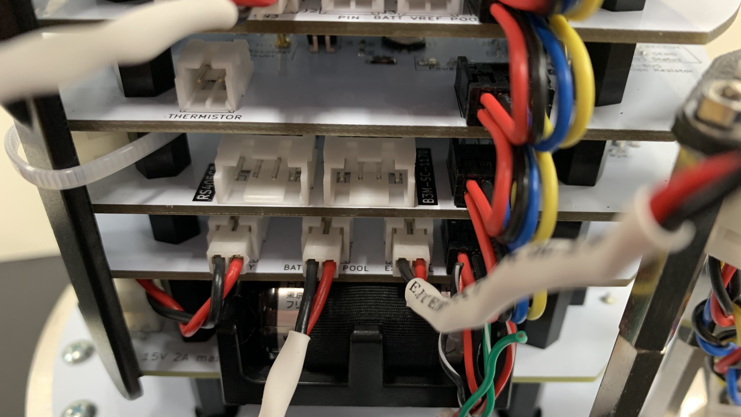
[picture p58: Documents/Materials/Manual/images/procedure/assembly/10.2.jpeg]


> VREF配線

1. 電源基板(15V) ----> 変圧基板(BATT)
2. --[VREF]--> 変圧基板(VREF)
3. アンビリカルケーブルコネクタ --[EXTERNAL]--> 変圧基板(EXTERNAL)

#### 10.3. バルブ制御モジュール基板の配線

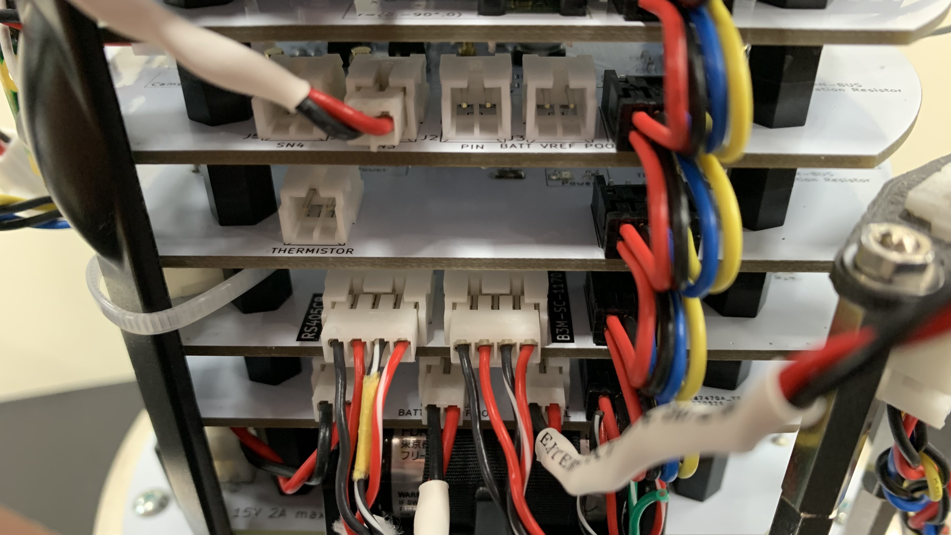
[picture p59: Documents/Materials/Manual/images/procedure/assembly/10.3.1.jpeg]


1. ----> バルブ制御モジュール基板(RS405CB)
2. ----> バルブ制御モジュール基板(B3M-SC-1170)

左は左、右は右。クロスしていなければ大丈夫。

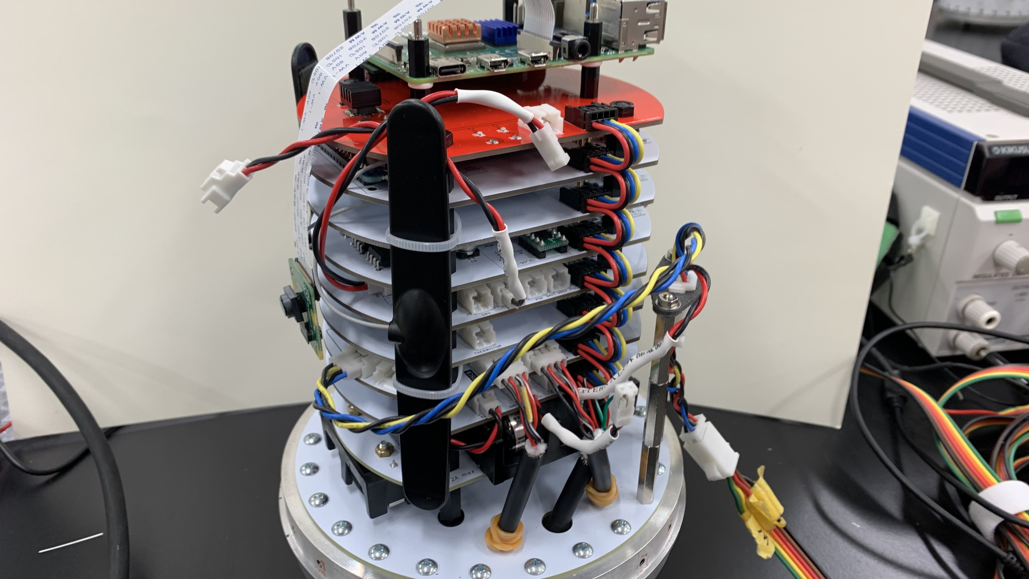
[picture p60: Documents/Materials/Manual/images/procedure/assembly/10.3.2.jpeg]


3. アンビリカルケーブルコネクタ ----> バルブ制御モジュール基板(Umbilical)

#### 10.4. 計測モジュール基板の配線

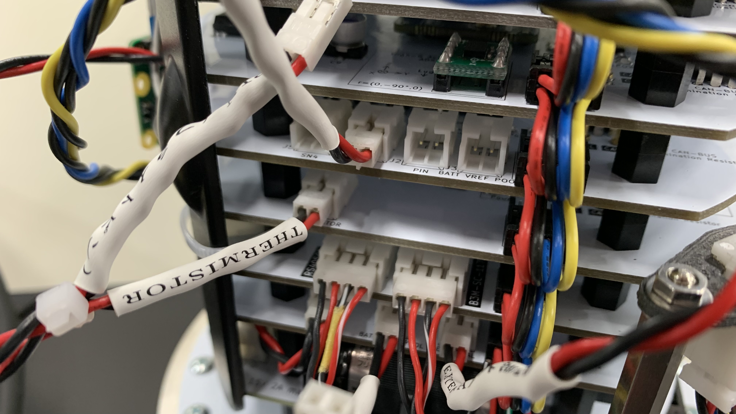
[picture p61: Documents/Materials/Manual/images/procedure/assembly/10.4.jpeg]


1. アンビリカルケーブルコネクタ --[THERMISTOR]--> 計測モジュール基板(THERMISTOR)

#### 10.5. フライトモジュール基板の配線

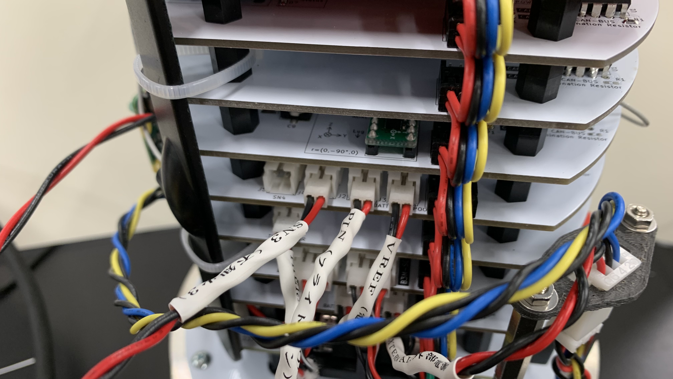
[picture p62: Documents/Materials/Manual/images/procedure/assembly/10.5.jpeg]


> SN3配線

1. --[SN3]--> フライトモジュール基板(SN3)
2. アンビリカルケーブルコネクタ --[PIN]--> フライトモジュール基板(PIN)
3. 変圧基板(VREF) --[VREF]--> フライトモジュール基板(VREF)

SN4は非接続です。

#### 10.6. カメラモジュール基板の配線

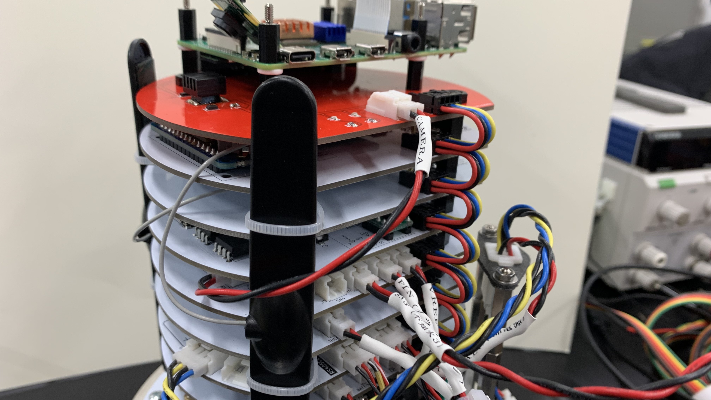
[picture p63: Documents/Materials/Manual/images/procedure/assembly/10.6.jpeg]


> CAMERA配線

1. フライトモジュール(CAMERA) --[CAMERA]--> カメラモジュール基板

## チェックリスト

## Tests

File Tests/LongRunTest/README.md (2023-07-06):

# ロングラン試験

電池が何分間もつかを検証する試験。

## 準備手順

1. FMと同仕様の計器タワーを組む。
   1. この時、電池は条件に合わせたものを使用する。
2. ログ出力のため、SystemDataCommunicationModuleには [/Tests/LongRunTest/Sources](./Sources/) の LogSender を書き込み、受信側には LogReceiver を書き込む。
3. 計器タワーをチューブ内に収める。
   1. チューブ内雰囲気温度計測用に計測モジュールから伸びるサーミスタをテープでどこにも触れないように固定する。

## 試験手順

1. 電源を投入する
2. 最初の1分間は10Hzで出力されるログを全て保存する。
3. 以降は10分経過ごとにログを記録する。
   1. 特に [Issue#71](https://github.com/tokai-student-rocket-project/H-58-Avionics/issues/71#issuecomment-1622992770) に示した最低動作電圧の目安に注意する。
4. 120分経過か電池切れにより全ての機器が正常に動作できなくなったら試験終了とする。

## 条件

試験は2種類の電池用いて1回づつ計2回行う。

Fujitsu製は今までのフライトで使用してきた電池である。Guangzhou Markyn Battery製は秋月電気通商で入手できる廉価版の電池であり、価格は1/4ほどに抑えられる。

### Fujitsu製電池

新品の`富士通 カメラ用リチウム電池 CR123A 3V 1300mAh`を5直列2並列で使用する。

### Guangzhou Markyn Battery製電池

新品の`Guangzhou Markyn Battery Co., Ltd. リチウム電池 CR123A 3V 1400mAh`を5直列2並列で使用する。

## 記録方法

LogReceiver から以下の情報を含むログがcsv形式で出力される。
- LogSender 動作開始からの経過時間 [ms]
- チューブ内雰囲気温度 [degC]
- 供給電圧 [V]
- バッテリー電圧 [V]
- プール電圧 [V]

最初の1分間はシリアルモニターのログを全てログファイルとして /Tests/LongRunTest/Logs/First.csv のパスに保存する。

以降は10分ごとにシリアルモニターを起動して以下の経過時間(millis)のパケットが含まれるように記録を行う。

| 経過時間 | millis |
| --- | --- |
| 10 min | 600,000 |
| 20 min | 1,200,000 |
| 30 min | 1,800,000 |
| 40 min | 2,400,000 |
| 50 min | 3,000,000 |
| 60 min | 3,600,000 |
| 70 min | 4,200,000 |
| 80 min | 4,800,000 |
| 90 min | 5,400,000 |
| 100 min  | 6,000,000 |
| 110 min  | 6,600,000 |
| 120 min  | 7,200,000 |
| 130 min  | 7,800,000 |
| 140 min  | 8,400,000 |
| 150 min  | 9,000,000 |

## 解析方法

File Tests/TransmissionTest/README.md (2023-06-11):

# 結果と考察

## 状況

日時: 6/7 18:14-18:31
天候: 晴れ (雲量6-8)

送信地点: 1号館屋上 (35.3657, 139.2732)
受信地点: 6号館屋上 (35.3608, 139.2729)
通信距離: 540 m

## 無線機概要

周波数: 921.8 MHz (LoRa 30ch)
送信電力: 20 mW
拡散率: 7
アンテナ高さ: 屋上から 1 m
アンテナ利得: 1 dBi

帯域幅: 125kHz, 250kHz, 500kHz (条件により変更)
データ長: 32Bytes, 64Bytes, 128Bytes (条件により変更)

## 条件

以下の7つの条件を設定する。

|条件|帯域幅|データ長|
|-|-|-|
|1|125 kHz|32 Bytes|
|2|125 kHz|64 Bytes|
|3|125 kHz|128 Bytes|
|4|250 kHz|32 Bytes|
|5|500 kHz|32 Bytes|
|6|500 kHz|64 Bytes|
|7|500 kHz|128 Bytes|

## 結果

各条件での計測結果を最頻値で示す。

|条件|受信強度 RSSI|送信回数|受信回数|N|
|-|-|-|-|-|
|1|-121 dBm|13.0 Hz|6.5 Hz|1545|
|2|-121 dBm|7.9 Hz|4 Hz|669|
|3|-100 dBm|4.5 Hz|2.2 Hz|191|
|4|-103 dBm|14.9 Hz|7.5 Hz|850|
|5|-104 dBm|43.5 Hz|21.7 Hz|3340|
|6|-105 dBm|26.3 Hz|13.3 Hz|1399|
|7|-103 dBm|15.2 Hz|7.5 Hz|1116|

なお、アンテナ高さを途中で変更しており、設定1,2は屋上から0m、設定3からは屋上から1mとなっている。

## 考察

### 受信強度

条件1,2での受信強度RSSIは-121dBm、条件3からは-100から-105dBmであり、結果から帯域幅は受信強度に影響しないと思われる。

実際、環境による擾乱を考慮しない自由空間での電波の伝搬損失量  $Loss$ (dB) は以下の式で表されるように、単に通信距離と周波数の関数となる。

$Loss$: 伝搬損失量 (dB), $d$: 通信距離 (m), $c$: 光速 ($2.998 \times 10^8$ m/s), $f$: 周波数 (MHz)

$$ Loss = 20 log (\frac{4 \pi d}{\lambda})$$

$$ \lambda = \frac{c}{f} $$

したがって、ロケット打ち上げにおけるダウンリンク及びアップリンクでは、通信速度改善のため帯域幅を広げることは受信強度の観点からは問題ないと考える。

### 送受信回数

送受信回数とは、規定のデータ長が含まれるパケットを1秒間に送信または受信できる回数を表している。これにはマイコン内での処理による遅延も影響する。

結果より帯域幅と送信回数及び、データ長と送信回数の関係がわかる。比較的狭い帯域幅では比例関係に近い関係があるといえる。一方、比較的広い帯域幅では、データ長が短い方が若干伝達効率が上がる結果となった。



また、受信回数が送信回数のほぼ半分の値になる現象が見られた。これについては今後検証を進める。

### まとめ

H-58搭載計器においては、帯域幅500kHzで64Bytes程度のデータをダウンリンクする場合10Hz程度の受信が可能であり、データを選定して32Bytes程度に抑えた場合は20Hz程度の受信が可能になる。GNSS情報を10Hzで更新することが可能になったことと合わせ、通信系の大幅な性能向上が見込める。

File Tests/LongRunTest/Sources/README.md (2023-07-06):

# LogSender.ino

ロングラン試験で必要な以下のログをLoRaで送信するためのコード。

- チューブ中雰囲気温度
- 供給電圧
- バッテリー電圧
- プール電圧

Arduino MKR WAN 1310 の SystemDataCommunicationModuleに書き込んで使う。

受信側の Arduino MKR WAN 1310 には LogReceiver.inoを書き込む。シリアルモニターにcsvで出力される。

GNSSなどSystemDataCommunicationModule本来の機能も動くので、消費電力的にはほとんど変わらないはず。

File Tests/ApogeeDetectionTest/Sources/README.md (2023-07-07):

# Subject.ino

SensingModule.inoから落下検知機能のみを取り出したコード

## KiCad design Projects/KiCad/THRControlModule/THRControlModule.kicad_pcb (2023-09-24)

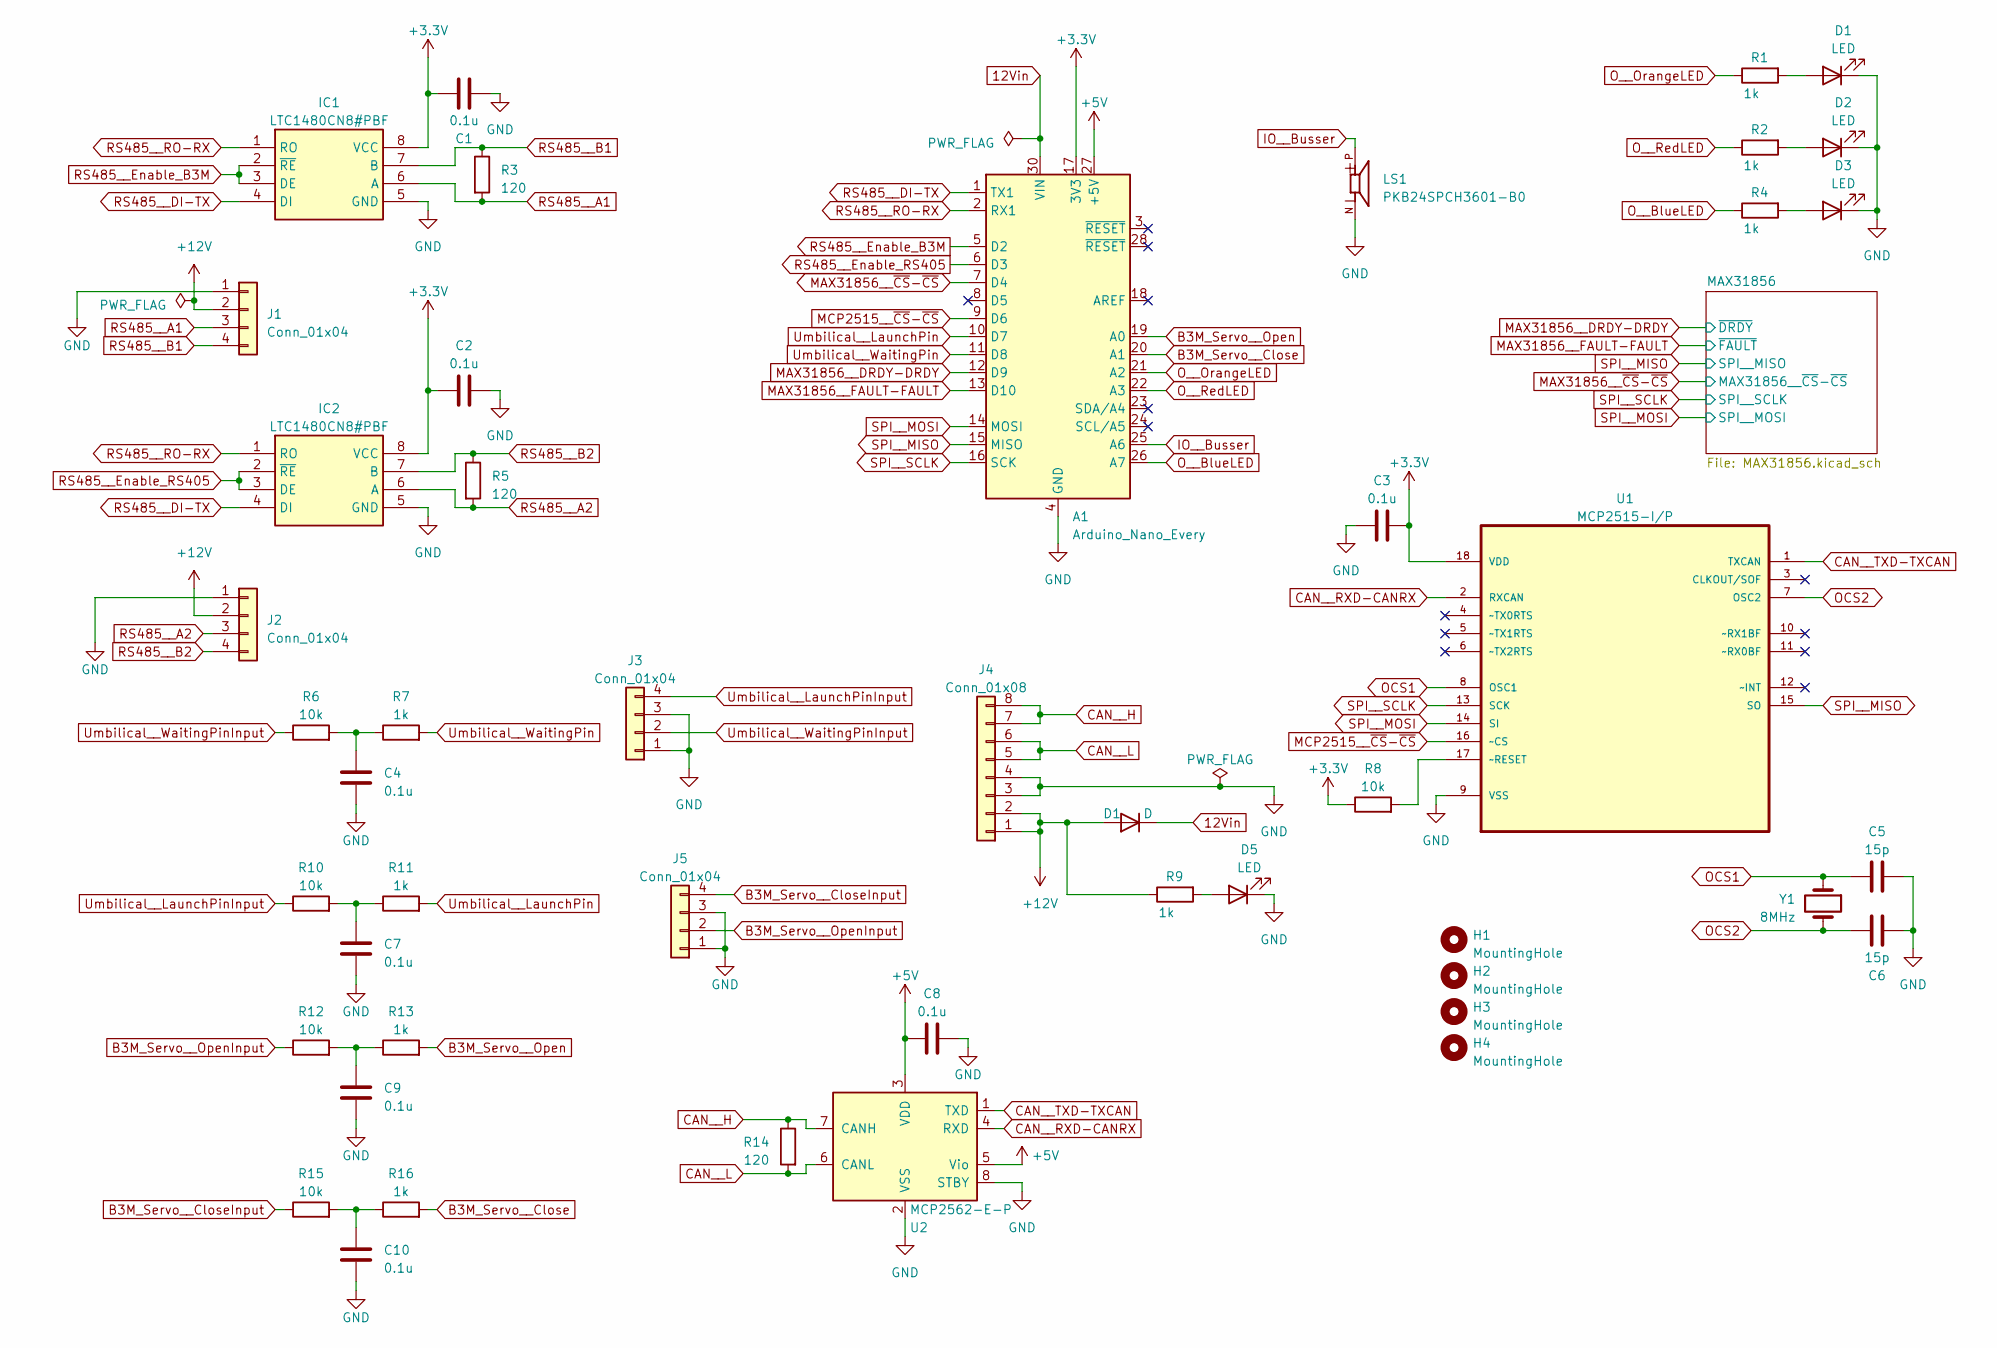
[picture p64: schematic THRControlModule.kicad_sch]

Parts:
A1: Arduino_Nano_Every; Arduino_Nano
C1, C2, C3, C4, C7, C8, C9, C10: 0.1u; C_0603_1608Metric_Pad1.08x0.95mm_HandSolder
C5, C6: 15p; C_0603_1608Metric_Pad1.08x0.95mm_HandSolder
D1: D; D_SOD-123
D2, D3, D5: LED; LED_0603_1608Metric_Pad1.05x0.95mm_HandSolder
H1, H2, H3, H4: MountingHole; MountingHole_4.5mm
IC1, IC2: LTC1480CN8#PBF; DIP794W53P254L1016H394Q8N; Manufacturer_Part_Number LTC1480CN8#PBF; Mouser Part Number 584-LTC1480CN8#PBF
J1, J2, J3, J5: Conn_01x04; Hirose_DF1BZ-4P-2.5DS
J4: Conn_01x08; Hirose_DF11B-8DP-2DS
LS1: PKB24SPCH3601-B0; SPKR_PKB24SPCH3601-B0; PARTREV March 24, 2017
R1, R2, R4, R7, R9, R11, R13, R16: 1k; R_0603_1608Metric_Pad0.98x0.95mm_HandSolder
R3, R5, R14: 120; R_0603_1608Metric_Pad0.98x0.95mm_HandSolder
R6, R8, R10, R12, R15: 10k; R_0603_1608Metric_Pad0.98x0.95mm_HandSolder
U1: MCP2515-I/P; DIP254P762X432-18; MPN MCP2515-I/P
U2: MCP2562-E-P; DIP-8_W7.62mm
Y1: 8MHz; Crystal_HC49-4H_Vertical

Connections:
+3.3V: A1.17 (3V3), C1.1, C2.1, C3.2, IC1.8 (VCC), IC2.8 (VCC), R8.1, U1.18 (VDD); also elsewhere on the board
+5V: A1.27 (+5V), C8.1, U2.3 (VDD), U2.5 (Vio)
B3M_Servo__Close: A1.20 (A1), R16.2
B3M_Servo__CloseInput: J5.4, R15.1
B3M_Servo__Open: A1.19 (A0), R13.2
B3M_Servo__OpenInput: J5.2, R12.1
CAN__H: J4.7, J4.8, R14.1, U2.7 (CANH)
CAN__L: J4.5, J4.6, R14.2, U2.6 (CANL)
CAN__RXD-CANRX: U1.2 (RXCAN), U2.4 (RXD)
CAN__TXD-TXCAN: U1.1 (TXCAN), U2.1 (TXD)
IO__Busser: A1.25 (A6), LS1.P
MAX31856__DRDY-DRDY: A1.12 (D9); also elsewhere on the board
MAX31856__FAULT-FAULT: A1.13 (D10); also elsewhere on the board
MAX31856__~CS-~CS: A1.7 (D4); also elsewhere on the board
MCP2515__~CS-~CS: A1.9 (D6), U1.16 (~CS)
unnamed: C4.1, R6.2, R7.1
unnamed: C7.1, R10.2, R11.1
unnamed: C9.1, R12.2, R13.1
unnamed: C10.1, R15.2, R16.1
unnamed: D2.2 (A), R2.2
unnamed: D3.2 (A), R4.2
unnamed: D5.2 (A), R9.2
unnamed: R8.2, U1.17 (~RESET)
OCS1: C5.1, U1.8 (OSC1), Y1.1
OCS2: C6.1, U1.7 (OSC2), Y1.2
O__BlueLED: A1.26 (A7), R4.1
O__OrangeLED: A1.21 (A2), R1.1
O__RedLED: A1.22 (A3), R2.1
RS485__A1: IC1.6 (A), J1.3, R3.2
RS485__A2: IC2.6 (A), J2.3, R5.2
RS485__B1: IC1.7 (B), J1.4, R3.1
RS485__B2: IC2.7 (B), J2.4, R5.1
RS485__DI-TX: A1.1 (TX1), IC1.4 (DI), IC2.4 (DI)
RS485__Enable_B3M: A1.5 (D2), IC1.2 (~RE), IC1.3 (DE)
RS485__Enable_RS405: A1.6 (D3), IC2.2 (~RE), IC2.3 (DE)
RS485__RO-RX: A1.2 (RX1), IC1.1 (RO), IC2.1 (RO)
SPI__MISO: A1.15 (MISO), U1.15 (SO); also elsewhere on the board
SPI__MOSI: A1.14 (MOSI), U1.14 (SI); also elsewhere on the board
SPI__SCLK: A1.16 (SCK), U1.13 (SCK); also elsewhere on the board
Umbilical__LaunchPin: A1.10 (D7), R11.2
Umbilical__LaunchPinInput: J3.4, R10.1
Umbilical__WaitingPin: A1.11 (D8), R7.2
Umbilical__WaitingPinInput: J3.2, R6.1

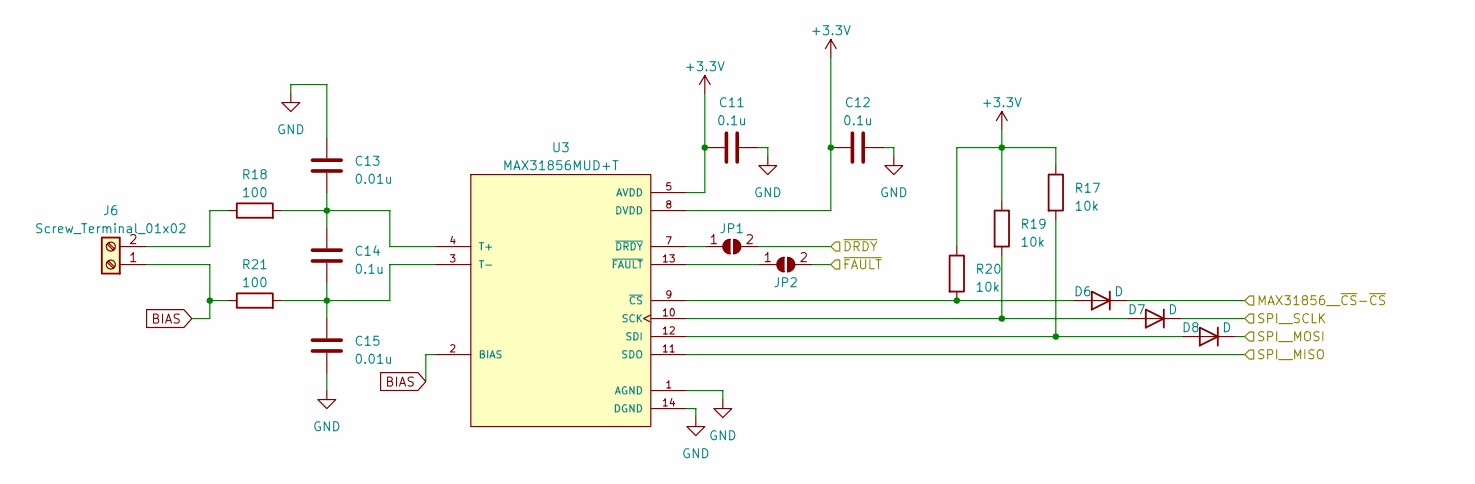
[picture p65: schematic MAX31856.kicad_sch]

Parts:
C11, C12, C14: 0.1u; C_0603_1608Metric_Pad1.08x0.95mm_HandSolder
C13, C15: 0.01u; C_0603_1608Metric_Pad1.08x0.95mm_HandSolder
D6, D7, D8: D; D_SOD-123
J6: Screw_Terminal_01x02; RS_PRO_611-8157
JP1, JP2: SolderJumper_2_Open; SolderJumper-2_P1.3mm_Open_Pad1.0x1.5mm
R17, R19, R20: 10k; R_0603_1608Metric_Pad0.98x0.95mm_HandSolder
R18, R21: 100; R_0805_2012Metric_Pad1.20x1.40mm_HandSolder
U3: MAX31856MUD+T; SOP65P640X110-14N; PARTREV 0

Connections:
+3.3V: C11.1, C12.1, R17.1, R19.1, R20.1, U3.5 (AVDD), U3.8 (DVDD); also elsewhere on the board
BIAS: J6.1, R21.1, U3.2 (BIAS)
MAX31856__DRDY-DRDY: JP1.2 (B); also elsewhere on the board
MAX31856__FAULT-FAULT: JP2.2 (B); also elsewhere on the board
MAX31856__~CS-~CS: D6.1 (K); also elsewhere on the board
unnamed: D6.2 (A), R20.2, U3.9 (~CS)
unnamed: D7.2 (A), R19.2, U3.10 (SCK)
unnamed: D8.2 (A), R17.2, U3.12 (SDI)
unnamed: J6.2, R18.1
unnamed: JP1.1 (A), U3.7 (~DRDY)
unnamed: JP2.1 (A), U3.13 (~FAULT)
unnamed: C13.2, C14.1, R18.2, U3.4 (T+)
unnamed: C14.2, C15.1, R21.2, U3.3 (T-)
SPI__MISO: U3.11 (SDO); also elsewhere on the board
SPI__MOSI: D8.1 (K); also elsewhere on the board
SPI__SCLK: D7.1 (K); also elsewhere on the board

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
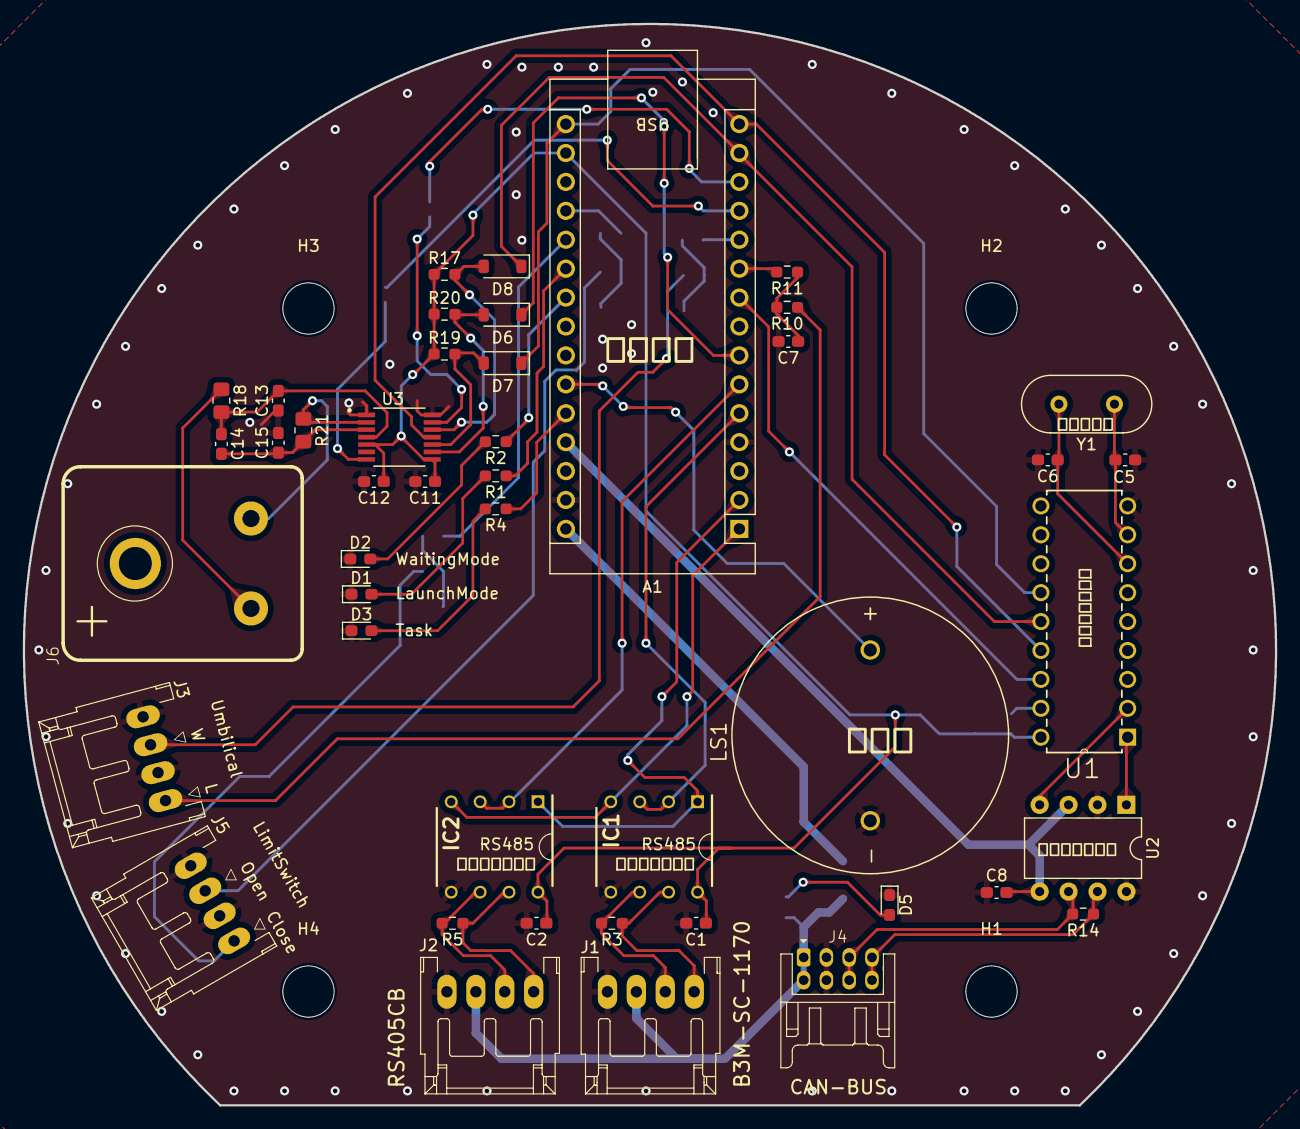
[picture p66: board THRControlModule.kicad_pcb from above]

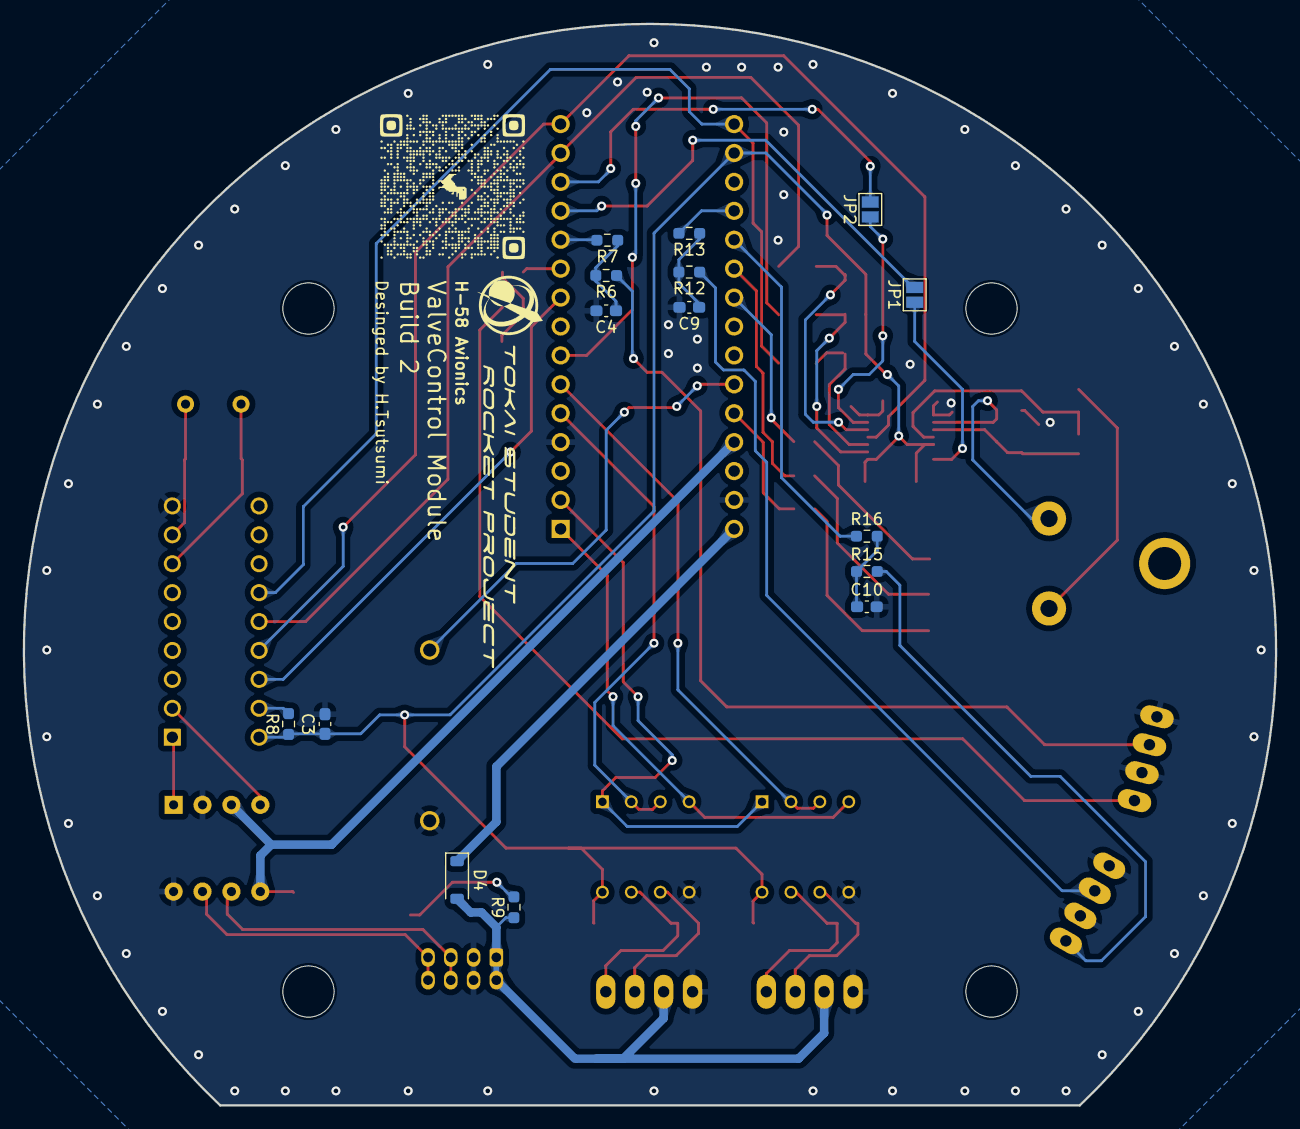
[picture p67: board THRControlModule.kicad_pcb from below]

Board: 2 copper layers, 110.0 x 95.0 mm, 64 parts (15 on the bottom side), 56 nets.

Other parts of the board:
D4: D; D_SOD-123

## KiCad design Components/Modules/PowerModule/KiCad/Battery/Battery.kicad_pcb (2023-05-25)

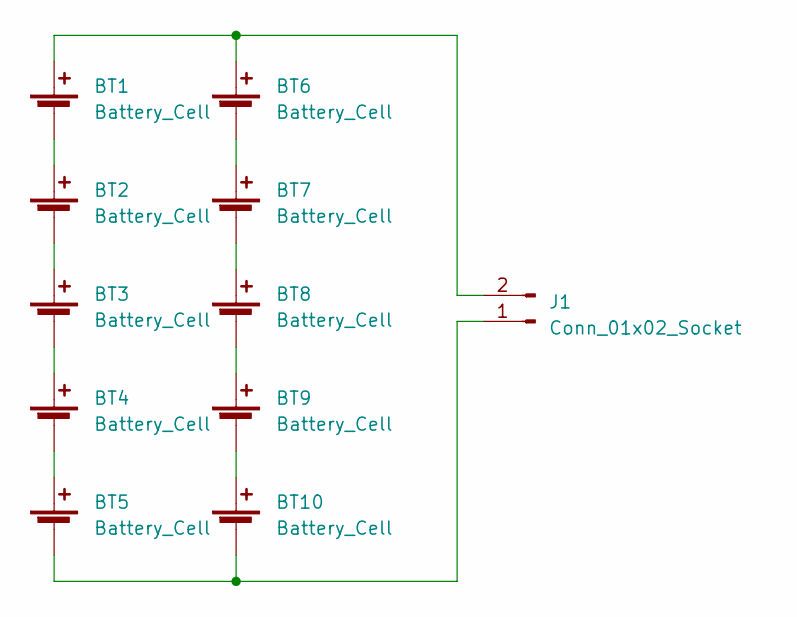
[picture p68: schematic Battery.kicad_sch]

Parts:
BT1, BT2, BT3, BT4, BT5, BT6, BT7, BT8, BT9, BT10: Battery_Cell; CR123APC
J1: Conn_01x02_Socket; CONNECTOR_2-STRAIGHT

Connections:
unnamed: BT1.1 (+), BT6.1 (+), J1.2
unnamed: BT1.2 (-), BT2.1 (+)
unnamed: BT2.2 (-), BT3.1 (+)
unnamed: BT3.2 (-), BT4.1 (+)
unnamed: BT4.2 (-), BT5.1 (+)
unnamed: BT6.2 (-), BT7.1 (+)
unnamed: BT7.2 (-), BT8.1 (+)
unnamed: BT8.2 (-), BT9.1 (+)
unnamed: BT9.2 (-), BT10.1 (+)
unnamed: BT5.2 (-), BT10.2 (-), J1.1

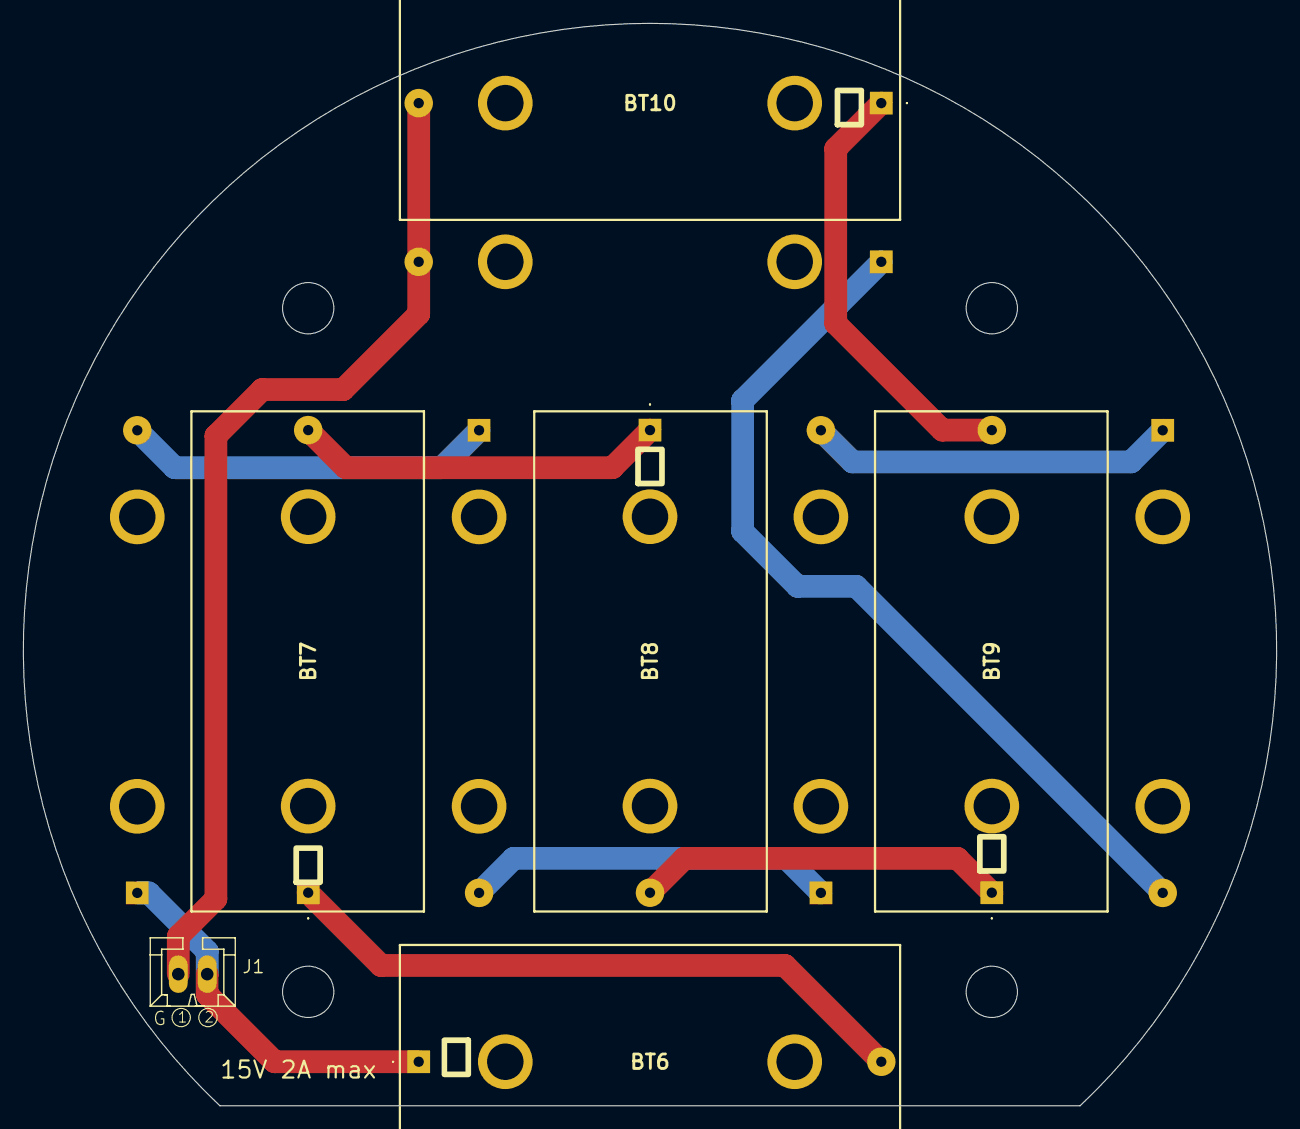
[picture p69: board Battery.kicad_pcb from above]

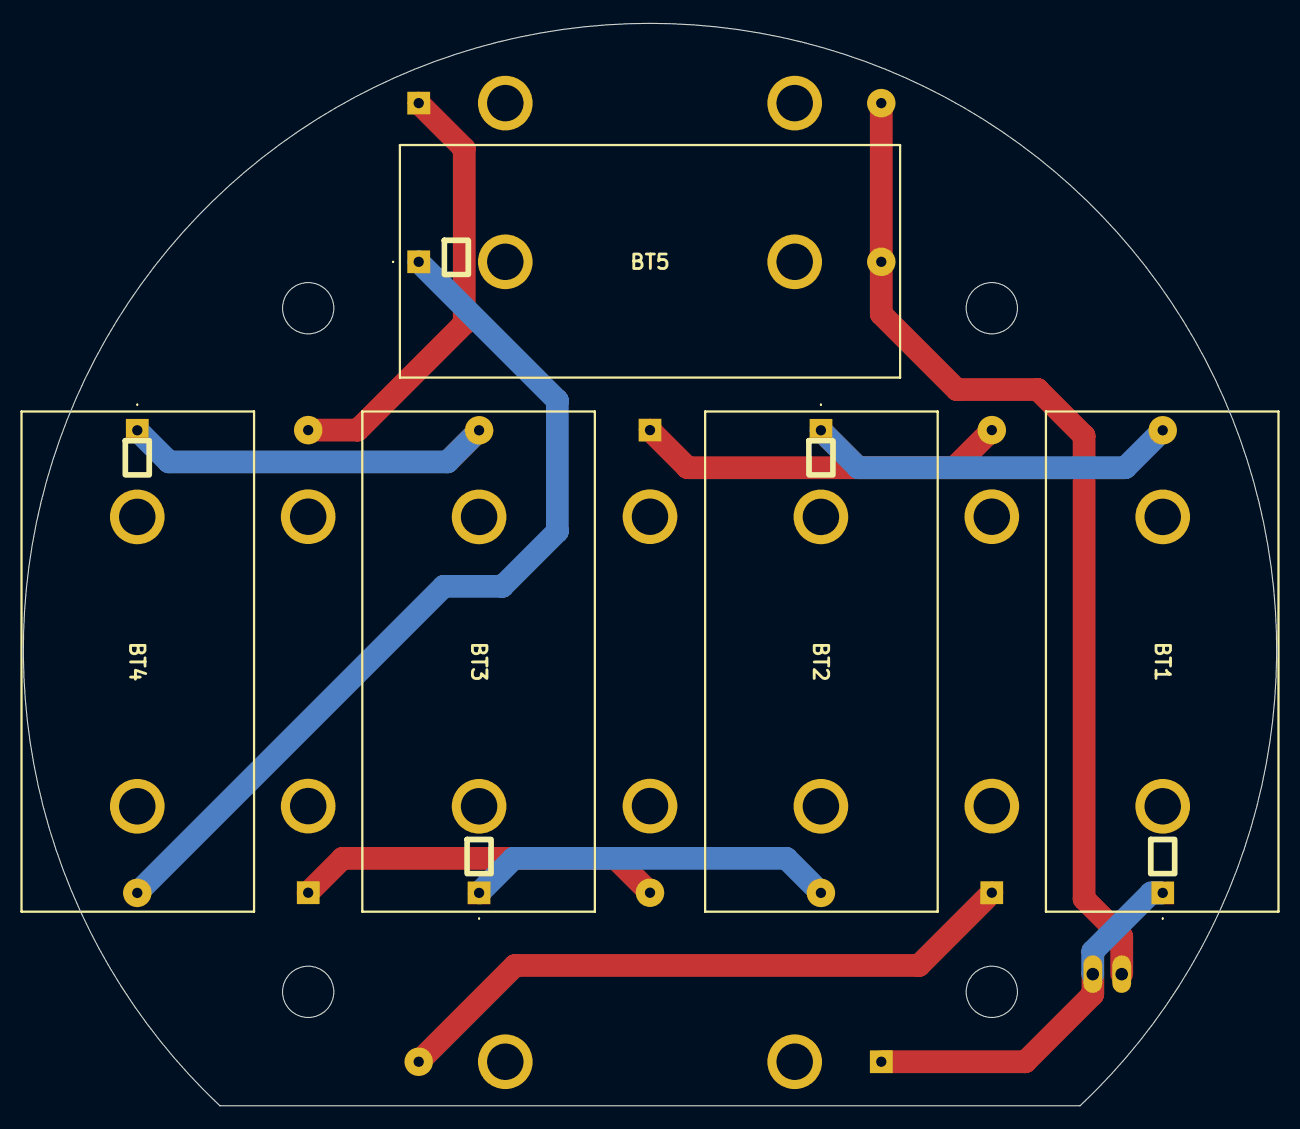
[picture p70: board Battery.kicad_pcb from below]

Board: 2 copper layers, 110.0 x 95.0 mm, 11 parts (5 on the bottom side), 10 nets.

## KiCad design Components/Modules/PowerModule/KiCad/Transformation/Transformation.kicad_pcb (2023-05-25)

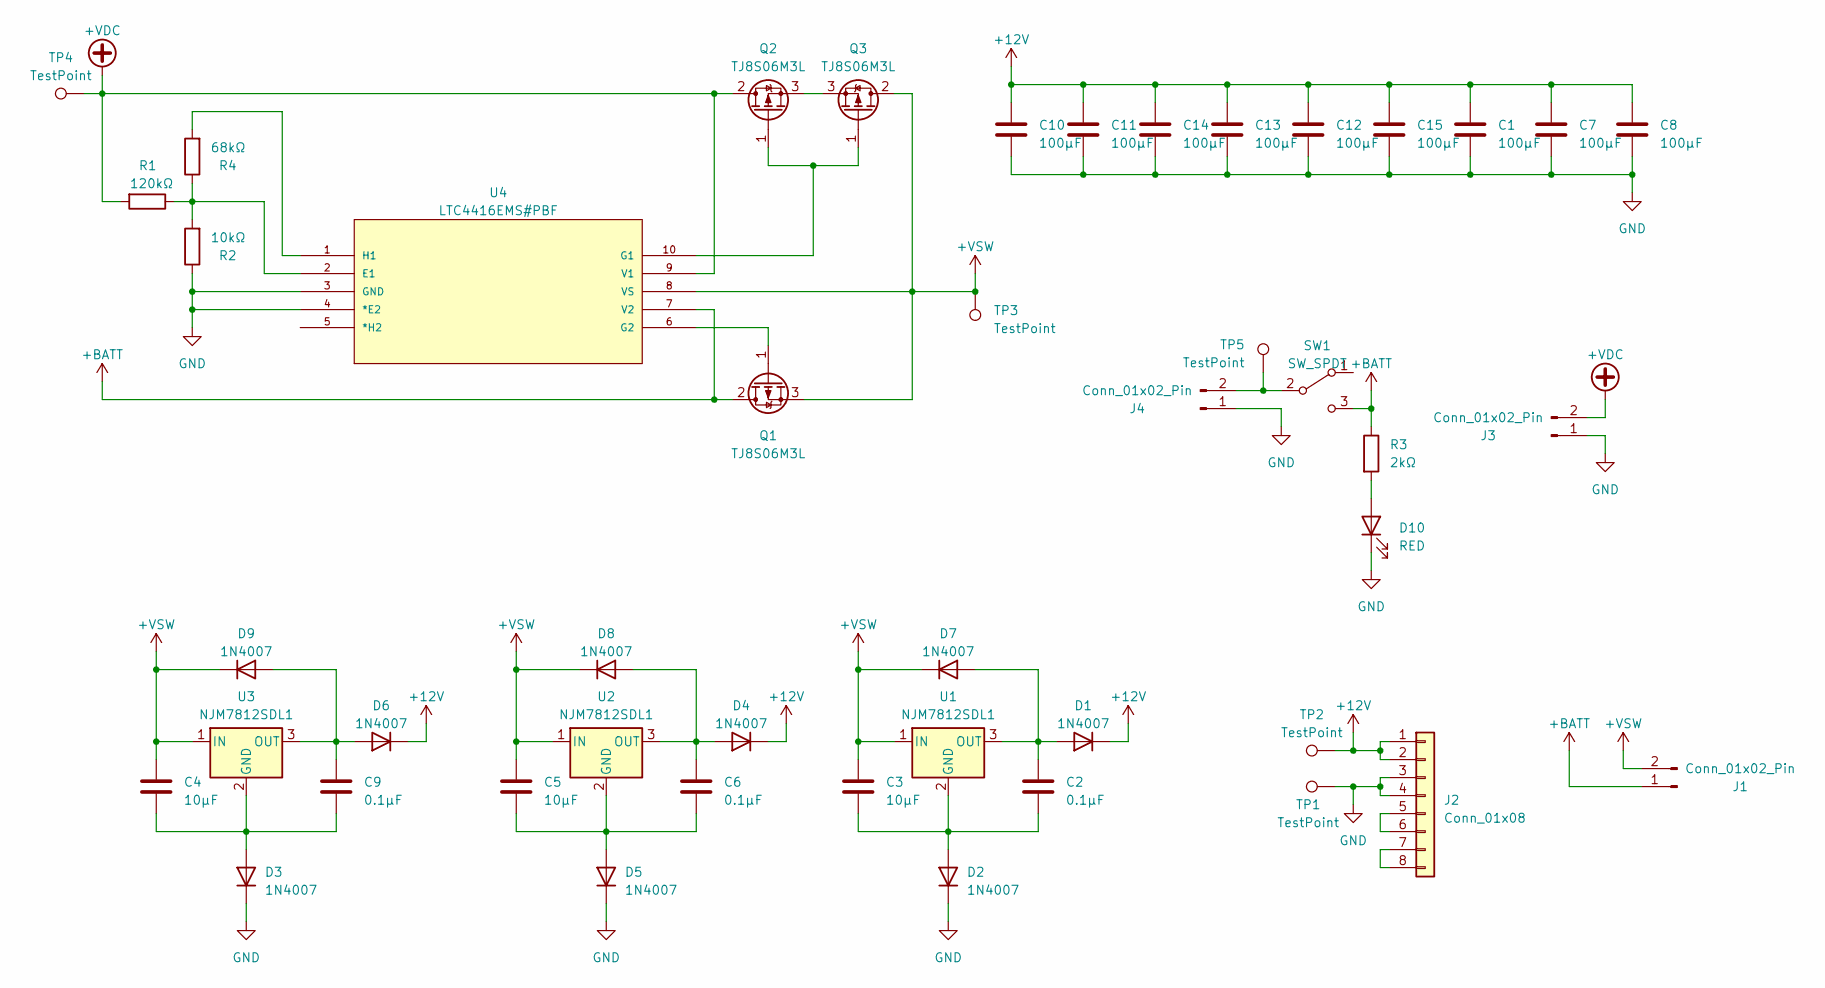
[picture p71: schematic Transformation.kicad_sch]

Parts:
C1, C7, C8, C10, C11, C12, C13, C14, C15: 100μF; CP_Elec_6.3x5.9
C2, C6, C9: 0.1μF; C_0603_1608Metric_Pad1.08x0.95mm_HandSolder
C3, C4, C5: 10μF; C_0603_1608Metric_Pad1.08x0.95mm_HandSolder
D1, D2, D3, D4, D5, D6, D7, D8, D9: 1N4007; D_SOD-123F
D10: RED; LED_0603_1608Metric_Pad1.05x0.95mm_HandSolder
J1, J3, J4: Conn_01x02_Pin; Hirose_DF1B
J2: Conn_01x08; Hirose_DF11B-8DP-2DS
Q1, Q2, Q3: TJ8S06M3L; TO-252-2
R1: 120kΩ; R_0805_2012Metric_Pad1.20x1.40mm_HandSolder
R2: 10kΩ; R_0805_2012Metric_Pad1.20x1.40mm_HandSolder
R3: 2kΩ; R_0603_1608Metric_Pad0.98x0.95mm_HandSolder
R4: 68kΩ; R_0603_1608Metric_Pad0.98x0.95mm_HandSolder
SW1: SW_SPDT; 2MS1T1B4M7QES
TP1, TP2, TP3, TP4, TP5: TestPoint; Pin_D1.0mm_L10.0mm
U1, U2, U3: NJM7812SDL1; TO-252-2
U4: LTC4416EMS#PBF; MSOP-10-1EP_3x3mm_P0.5mm_EP1.73x1.98mm; MANUFACTURER_PART_NUMBER ltc4416ims1

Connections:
+12V: C1.1, C7.1, C8.1, C10.1, C11.1, C12.1, C13.1, C14.1, C15.1, D1.1 (K), D4.1 (K), D6.1 (K), J2.1, J2.2, TP2.1
+BATT: J1.1, Q1.2 (D), R3.1, SW1.3 (C), U4.7 (V2)
+VDC: J3.2, Q2.2 (D), R1.2, TP4.1, U4.9 (V1)
+VSW: C3.1, C4.1, C5.1, D7.1 (K), D8.1 (K), D9.1 (K), J1.2, Q1.3 (S), Q3.2 (D), TP3.1, U1.1 (IN), U2.1 (IN), U3.1 (IN), U4.8 (VS)
GND: C1.2, C7.2, C8.2, C10.2, C11.2, C12.2, C13.2, C14.2, C15.2, D2.1 (K), D3.1 (K), D5.1 (K), D10.1 (K), J2.3, J2.4, J3.1, J4.1, R2.1, TP1.1, U4.3 (GND), U4.4 (*E2), U4.11
unnamed: C2.1, D1.2 (A), D7.2 (A), U1.3 (OUT)
unnamed: C2.2, C3.2, D2.2 (A), U1.2 (GND)
unnamed: C4.2, C9.2, D3.2 (A), U3.2 (GND)
unnamed: C6.1, D4.2 (A), D8.2 (A), U2.3 (OUT)
unnamed: C5.2, C6.2, D5.2 (A), U2.2 (GND)
unnamed: C9.1, D6.2 (A), D9.2 (A), U3.3 (OUT)
unnamed: D10.2 (A), R3.2
unnamed: J2.5, J2.6
unnamed: J2.7, J2.8
unnamed: J4.2, SW1.2 (B), TP5.1
unnamed: Q1.1 (G), U4.6 (G2)
unnamed: Q2.1 (G), Q3.1 (G), U4.10 (G1)
unnamed: Q2.3 (S), Q3.3 (S)
unnamed: R1.1, R2.2, R4.1, U4.2 (E1)
unnamed: R4.2, U4.1 (H1)

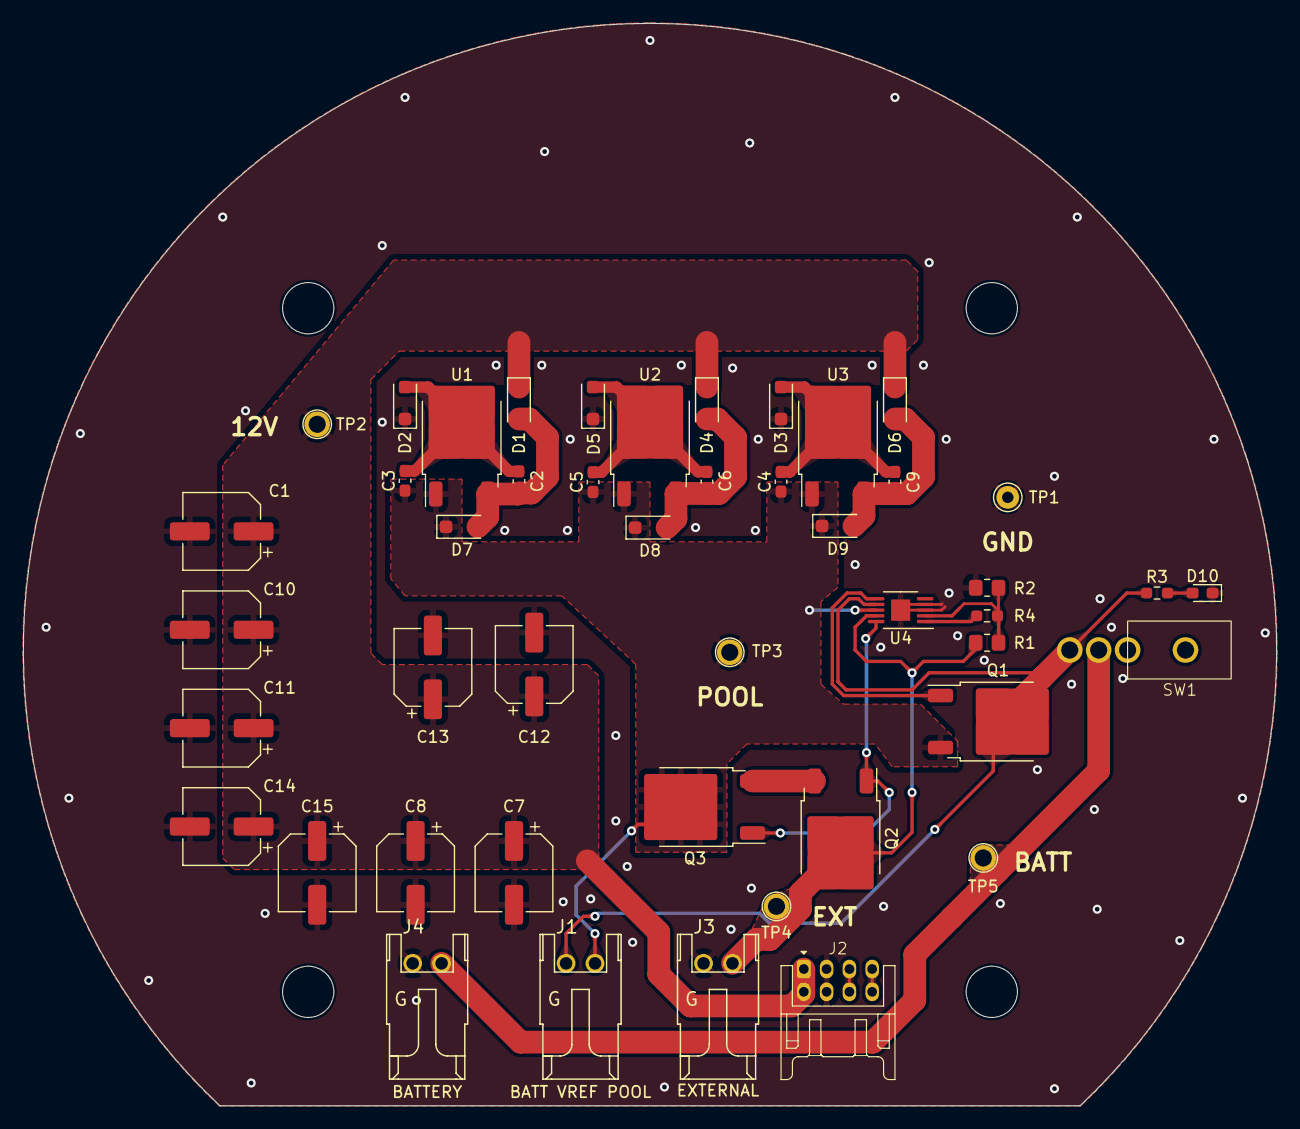
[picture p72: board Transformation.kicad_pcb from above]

Board: 2 copper layers, 110.0 x 95.0 mm, 46 parts (0 on the bottom side), 20 nets.

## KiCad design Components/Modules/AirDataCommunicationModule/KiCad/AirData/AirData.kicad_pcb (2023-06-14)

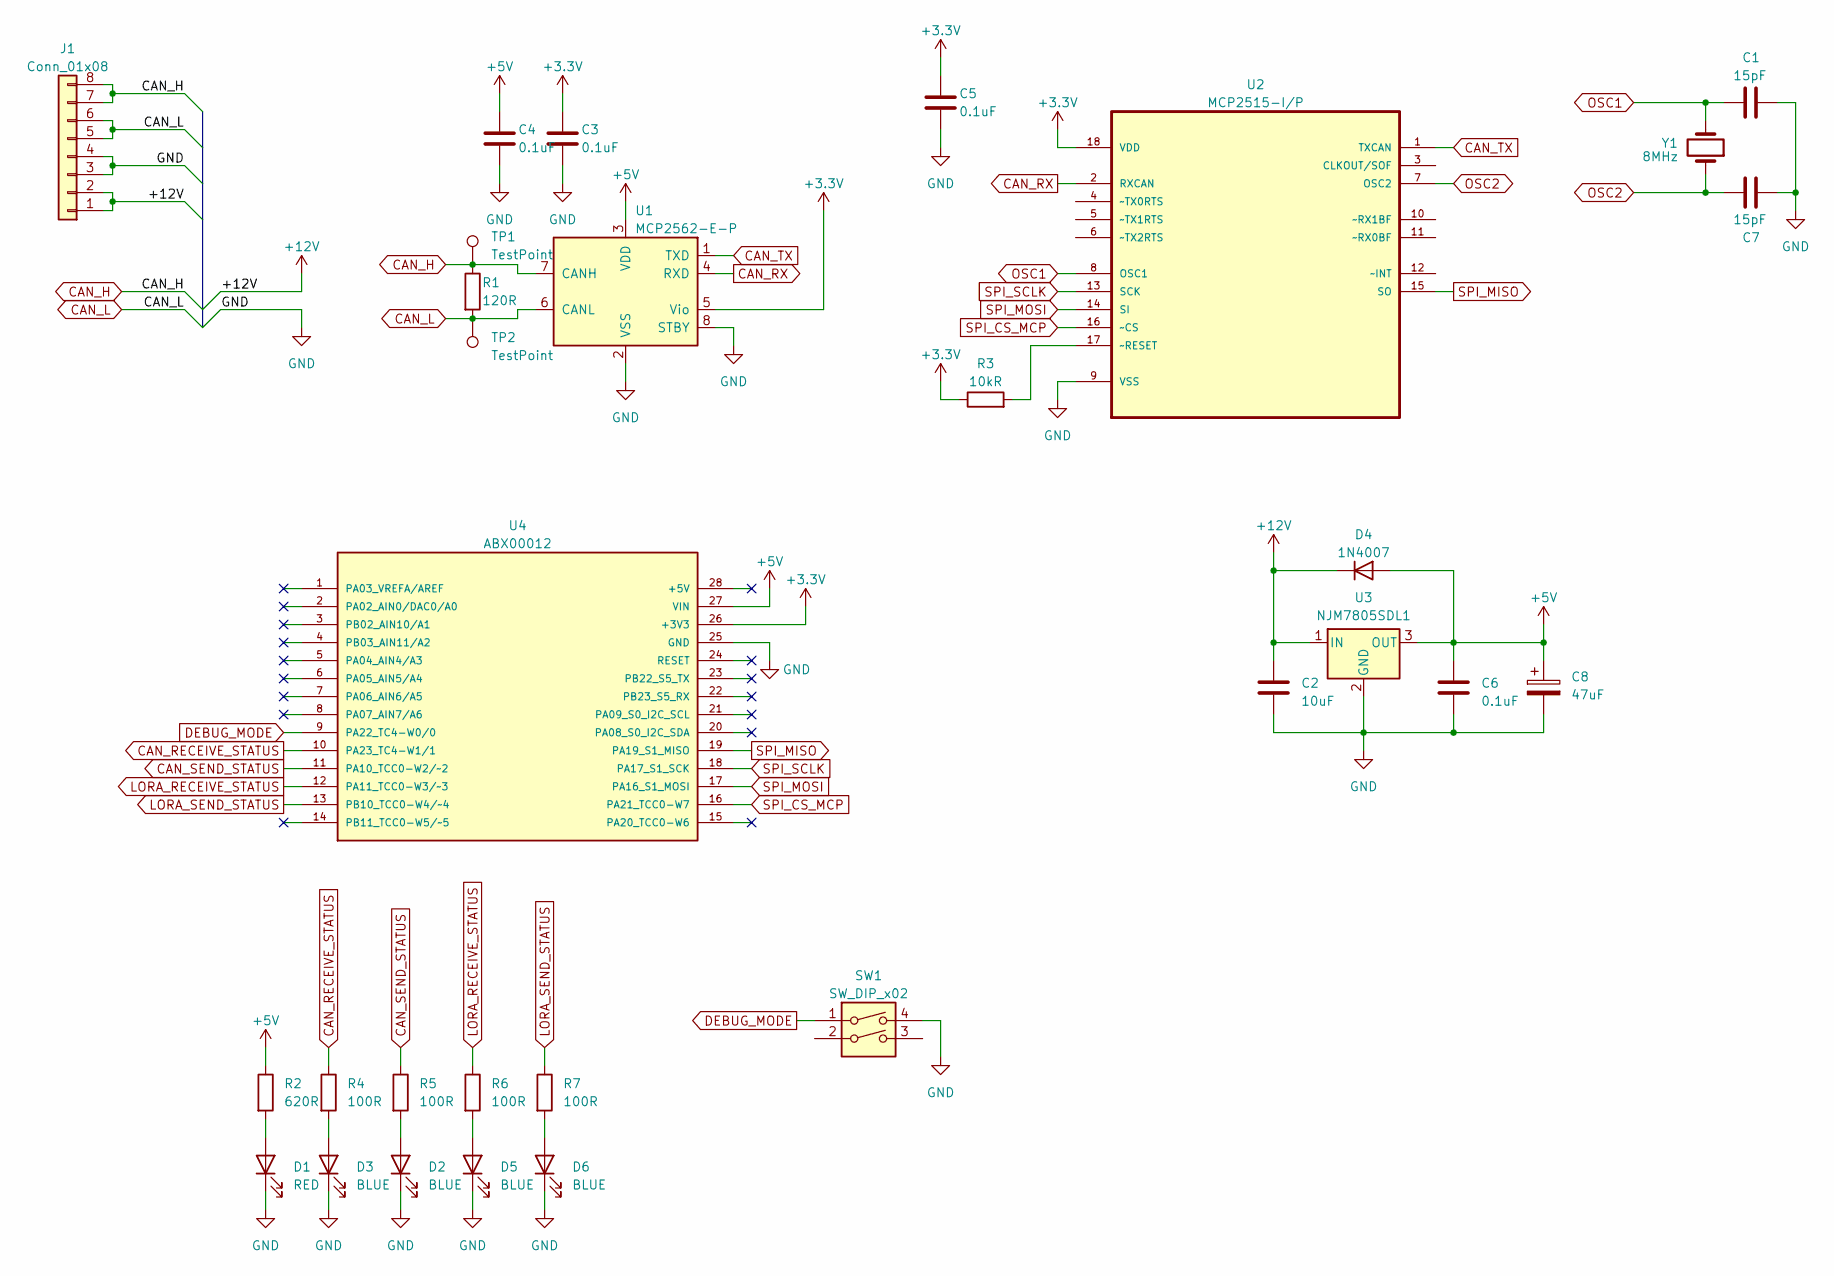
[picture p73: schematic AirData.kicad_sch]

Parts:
C1, C7: 15pF; C_0603_1608Metric_Pad1.08x0.95mm_HandSolder
C2: 10uF; C_0603_1608Metric_Pad1.08x0.95mm_HandSolder
C3, C4, C5, C6: 0.1uF; C_0603_1608Metric_Pad1.08x0.95mm_HandSolder
C8: 47uF; CP_Elec_6.3x5.9
D1: RED; LED_0603_1608Metric_Pad1.05x0.95mm_HandSolder
D2, D3, D5, D6: BLUE; LED_0603_1608Metric_Pad1.05x0.95mm_HandSolder
D4: 1N4007; D_SOD-123F
J1: Conn_01x08; Hirose_DF11B-8DP-2DS
R1: 120R; R_0603_1608Metric_Pad0.98x0.95mm_HandSolder
R2: 620R; R_0603_1608Metric_Pad0.98x0.95mm_HandSolder
R3: 10kR; R_0805_2012Metric_Pad1.20x1.40mm_HandSolder
R4, R5, R6, R7: 100R; R_0805_2012Metric_Pad1.20x1.40mm_HandSolder
SW1: SW_DIP_x02; SW_DIP_SPSTx02_Piano_10.8x6.64mm_W7.62mm_P2.54mm
TP1, TP2: TestPoint; Pin_D1.0mm_L10.0mm
U1: MCP2562-E-P; DIP-8_W7.62mm
U2: MCP2515-I/P; DIP-18_W7.62mm; MPN MCP2515-I/P
U3: NJM7805SDL1; TO-252-2
U4: ABX00012; ARDUINO_ABX00012; PARTREV 5
Y1: 8MHz; Crystal_SMD_HC49-SD

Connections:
+3.3V: C3.1, C5.1, R3.1, U1.5 (Vio), U2.18 (VDD), U4.26 (+3V3)
+5V: C4.1, C6.1, C8.1, D4.2 (A), R2.1, U1.3 (VDD), U3.3 (OUT), U4.27 (VIN)
+12V: C2.1, D4.1 (K), J1.1, J1.2, U3.1 (IN)
CAN_H: J1.7, J1.8, R1.1, TP1.1, U1.7 (CANH)
CAN_L: J1.5, J1.6, R1.2, TP2.1, U1.6 (CANL)
CAN_RECEIVE_STATUS: R4.1, U4.10 (PA23_TC4-W1/1)
CAN_RX: U1.4 (RXD), U2.2 (RXCAN)
CAN_SEND_STATUS: R5.1, U4.11 (PA10_TCC0-W2/~2)
CAN_TX: U1.1 (TXD), U2.1 (TXCAN)
DEBUG_MODE: SW1.1, U4.9 (PA22_TC4-W0/0)
GND: C1.1, C2.2, C3.2, C4.2, C5.2, C6.2, C7.1, C8.2, D1.1 (K), D2.1 (K), D3.1 (K), D5.1 (K), D6.1 (K), J1.3, J1.4, SW1.4, U1.2 (VSS), U1.8 (STBY), U2.9 (VSS), U3.2 (GND), U4.25 (GND)
LORA_RECEIVE_STATUS: R6.1, U4.12 (PA11_TCC0-W3/~3)
LORA_SEND_STATUS: R7.1, U4.13 (PB10_TCC0-W4/~4)
unnamed: D1.2 (A), R2.2
unnamed: D2.2 (A), R5.2
unnamed: D3.2 (A), R4.2
unnamed: D5.2 (A), R6.2
unnamed: D6.2 (A), R7.2
unnamed: R3.2, U2.17 (~RESET)
OSC1: C1.2, U2.8 (OSC1), Y1.2
OSC2: C7.2, U2.7 (OSC2), Y1.1
SPI_CS_MCP: U2.16 (~CS), U4.16 (PA21_TCC0-W7)
SPI_MISO: U2.15 (SO), U4.19 (PA19_S1_MISO)
SPI_MOSI: U2.14 (SI), U4.17 (PA16_S1_MOSI)
SPI_SCLK: U2.13 (SCK), U4.18 (PA17_S1_SCK)

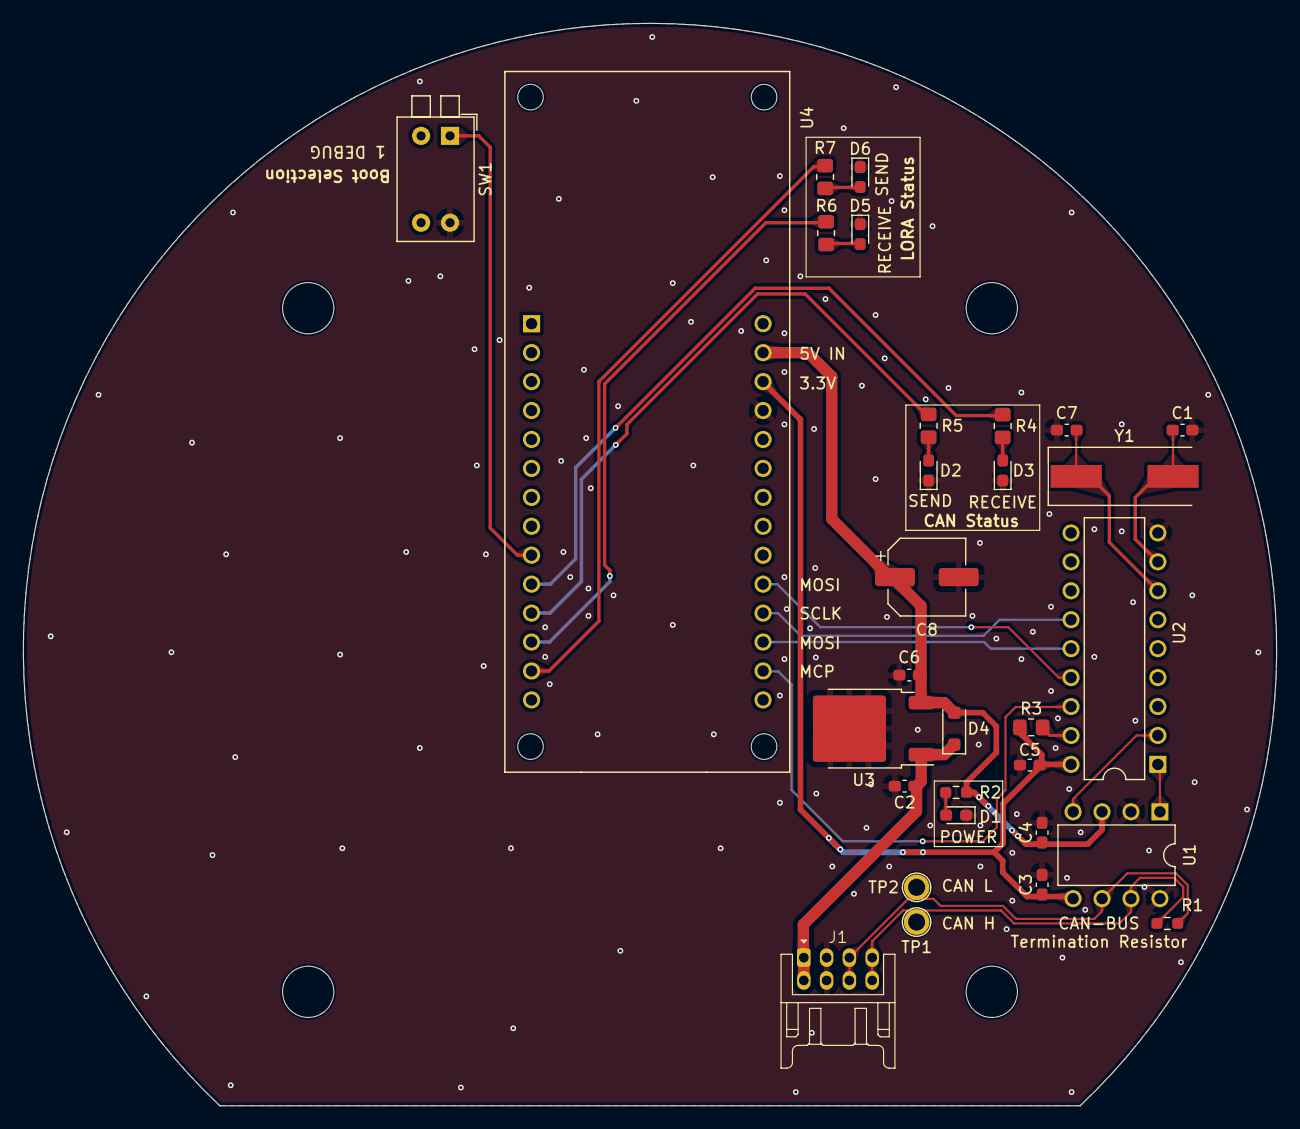
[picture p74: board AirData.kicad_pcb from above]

Board: 2 copper layers, 110.0 x 95.0 mm, 30 parts (0 on the bottom side), 25 nets.

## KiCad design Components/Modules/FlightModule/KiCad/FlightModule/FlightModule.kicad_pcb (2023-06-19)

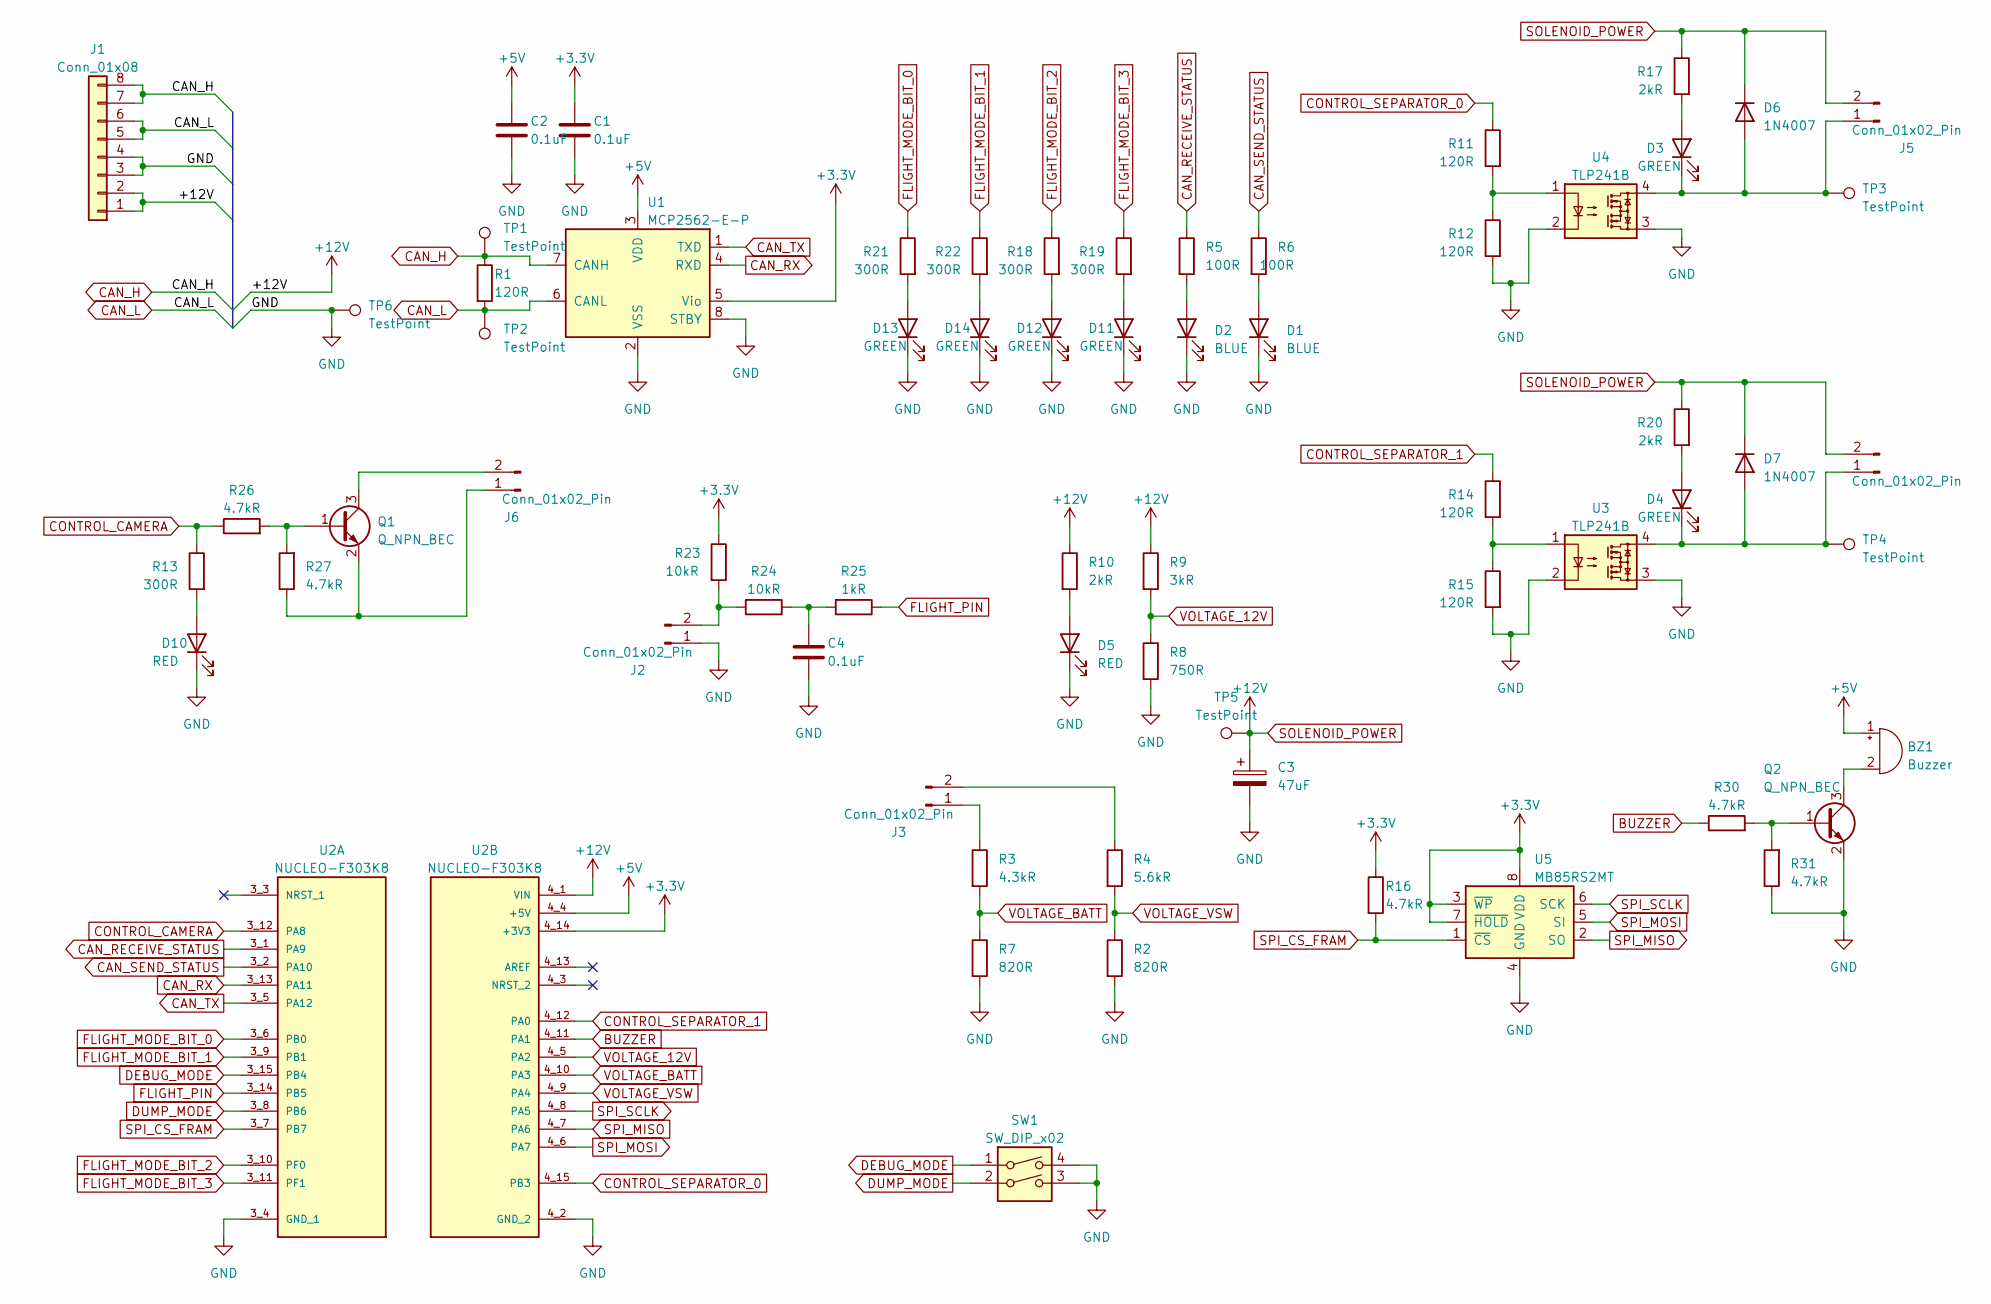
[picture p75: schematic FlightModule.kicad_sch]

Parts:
BZ1: Buzzer; Buzzer_12x9.5RM7.6
C1, C2, C4: 0.1uF; C_0603_1608Metric_Pad1.08x0.95mm_HandSolder
C3: 47uF; CP_Elec_6.3x5.9
D1, D2: BLUE; LED_0603_1608Metric_Pad1.05x0.95mm_HandSolder
D3, D4, D11, D12, D13, D14: GREEN; LED_0603_1608Metric_Pad1.05x0.95mm_HandSolder
D5, D10: RED; LED_0603_1608Metric_Pad1.05x0.95mm_HandSolder
D6, D7: 1N4007; D_SOD-123F
J1: Conn_01x08; Hirose_DF11B-8DP-2DS
J2, J3, J4, J5, J6: Conn_01x02_Pin; Hirose_DF1B
Q1, Q2: Q_NPN_BEC; SC-59_Handsoldering
R1, R11, R12, R14, R15: 120R; R_0603_1608Metric_Pad0.98x0.95mm_HandSolder
R2, R7: 820R; R_0603_1608Metric_Pad0.98x0.95mm_HandSolder
R3: 4.3kR; R_0603_1608Metric_Pad0.98x0.95mm_HandSolder
R4: 5.6kR; R_0603_1608Metric_Pad0.98x0.95mm_HandSolder
R5, R6: 100R; R_0805_2012Metric_Pad1.20x1.40mm_HandSolder
R8: 750R; R_0603_1608Metric_Pad0.98x0.95mm_HandSolder
R9: 3kR; R_0603_1608Metric_Pad0.98x0.95mm_HandSolder
R10, R17, R20: 2kR; R_0603_1608Metric_Pad0.98x0.95mm_HandSolder
R13, R18, R19, R21, R22: 300R; R_0603_1608Metric_Pad0.98x0.95mm_HandSolder
R16, R26, R27, R30, R31: 4.7kR; R_0603_1608Metric_Pad0.98x0.95mm_HandSolder
R23, R24: 10kR; R_0805_2012Metric_Pad1.20x1.40mm_HandSolder
R25: 1kR; R_0603_1608Metric_Pad0.98x0.95mm_HandSolder
SW1: SW_DIP_x02; SW_DIP_SPSTx02_Piano_10.8x6.64mm_W7.62mm_P2.54mm
TP1, TP2, TP3, TP4, TP5, TP6: TestPoint; Pin_D1.0mm_L10.0mm
U1: MCP2562-E-P; DIP-8_W7.62mm
U2: NUCLEO-F303K8; MODULE_NUCLEO-F303K8; PARTREV 5
U3, U4: TLP241B; DIP-4_W7.62mm
U5: MB85RS2MT; DIP-8_W7.62mm

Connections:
+3.3V: C1.1, R16.1, R23.1, U1.5 (Vio), U2.4_14 (+3V3), U5.3 (~WP), U5.7 (~HOLD), U5.8 (VDD)
+5V: BZ1.1 (-), C2.1, U1.3 (VDD), U2.4_4 (+5V)
BUZZER: R30.1, U2.4_11 (PA1)
CAN_H: J1.7, J1.8, R1.1, TP1.1, U1.7 (CANH)
CAN_L: J1.5, J1.6, R1.2, TP2.1, U1.6 (CANL)
CAN_RECEIVE_STATUS: R5.1, U2.3_1 (PA9)
CAN_RX: U1.4 (RXD), U2.3_13 (PA11)
CAN_SEND_STATUS: R6.1, U2.3_2 (PA10)
CAN_TX: U1.1 (TXD), U2.3_5 (PA12)
CONTROL_CAMERA: R13.1, R26.1, U2.3_12 (PA8)
CONTROL_SEPARATOR_0: R11.1, U2.4_15 (PB3)
CONTROL_SEPARATOR_1: R14.1, U2.4_12 (PA0)
DEBUG_MODE: SW1.1, U2.3_15 (PB4)
DUMP_MODE: SW1.2, U2.3_8 (PB6)
FLIGHT_MODE_BIT_0: R21.1, U2.3_6 (PB0)
FLIGHT_MODE_BIT_1: R22.1, U2.3_9 (PB1)
FLIGHT_MODE_BIT_2: R18.1, U2.3_10 (PF0)
FLIGHT_MODE_BIT_3: R19.1, U2.3_11 (PF1)
FLIGHT_PIN: R25.1, U2.3_14 (PB5)
GND: C1.2, C2.2, C3.2, C4.2, D1.1 (K), D2.1 (K), D5.1 (K), D10.1 (K), D11.1 (K), D12.1 (K), D13.1 (K), D14.1 (K), J1.3, J1.4, J2.1, Q2.2 (E), R2.2, R7.2, R8.2, R12.2, R15.2, R31.1, SW1.3, SW1.4, TP6.1, U1.2 (VSS), U1.8 (STBY), U2.3_4 (GND_1), U2.4_2 (GND_2), U3.2, U3.3, U4.2, U4.3, U5.4 (GND)
unnamed: BZ1.2 (+), Q2.3 (C)
unnamed: C4.1, R24.1, R25.2
unnamed: D1.2 (A), R6.2
unnamed: D2.2 (A), R5.2
unnamed: D3.2 (A), R17.2
unnamed: D3.1 (K), D6.2 (A), J5.1, TP3.1, U4.4
unnamed: D4.2 (A), R20.2
unnamed: D4.1 (K), D7.2 (A), J4.1, TP4.1, U3.4
unnamed: D5.2 (A), R10.2
unnamed: D10.2 (A), R13.2
unnamed: D11.2 (A), R19.2
unnamed: D12.2 (A), R18.2
unnamed: D13.2 (A), R21.2
unnamed: D14.2 (A), R22.2
unnamed: J2.2, R23.2, R24.2
unnamed: J3.1, R3.1
unnamed: J3.2, R4.1
unnamed: J6.1, Q1.2 (E), R27.1
unnamed: J6.2, Q1.3 (C)
unnamed: Q1.1 (B), R26.2, R27.2
unnamed: Q2.1 (B), R30.2, R31.2
unnamed: R11.2, R12.1, U4.1
unnamed: R14.2, R15.1, U3.1
SOLENOID_POWER: C3.1, D6.1 (K), D7.1 (K), J1.1, J1.2, J4.2, J5.2, R9.1, R10.1, R17.1, R20.1, TP5.1, U2.4_1 (VIN)
SPI_CS_FRAM: R16.2, U2.3_7 (PB7), U5.1 (~CS)
SPI_MISO: U2.4_7 (PA6), U5.2 (SO)
SPI_MOSI: U2.4_6 (PA7), U5.5 (SI)
SPI_SCLK: U2.4_8 (PA5), U5.6 (SCK)
VOLTAGE_12V: R8.1, R9.2, U2.4_5 (PA2)
VOLTAGE_BATT: R3.2, R7.1, U2.4_10 (PA3)
VOLTAGE_VSW: R2.1, R4.2, U2.4_9 (PA4)


Board: 2 copper layers, 110.0 x 95.0 mm, 67 parts (0 on the bottom side), 51 nets.

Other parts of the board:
e: MountingHole_4.5mm

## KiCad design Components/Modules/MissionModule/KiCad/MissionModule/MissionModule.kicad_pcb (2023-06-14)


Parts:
C1, C6: 15pF; C_0603_1608Metric_Pad1.08x0.95mm_HandSolder
C2, C4, C5, C7: 0.1uF; C_0603_1608Metric_Pad1.08x0.95mm_HandSolder
C3: 10uF; C_0603_1608Metric_Pad1.08x0.95mm_HandSolder
C8, C9: 47uF; CP_Elec_6.3x5.9
D1, D9: RED; LED_0603_1608Metric_Pad1.05x0.95mm_HandSolder
D2: 1N4007; D_SOD-123F
D3, D4, D5, D6: BLUE; LED_0603_1608Metric_Pad1.05x0.95mm_HandSolder
D7, D8: GREEN; LED_0603_1608Metric_Pad1.05x0.95mm_HandSolder
F1: Polyfuse; Fuse_1206_3216Metric_Pad1.42x1.75mm_HandSolder
J1: Conn_01x08; Hirose_DF11B-8DP-2DS
J2: Micro_SD_Card_Det_Hirose_DM3AT; microSD_HC_Hirose_DM3AT-SF-PEJM5
R1, R8, R10: 120R; R_0603_1608Metric_Pad0.98x0.95mm_HandSolder
R2: 620R; R_0603_1608Metric_Pad0.98x0.95mm_HandSolder
R3: 10kR; R_0805_2012Metric_Pad1.20x1.40mm_HandSolder
R4, R5, R6, R7: 100R; R_0805_2012Metric_Pad1.20x1.40mm_HandSolder
R9, R11, R15: 300R; R_0603_1608Metric_Pad0.98x0.95mm_HandSolder
R12, R13, R14, R16: 4.7kR; R_0603_1608Metric_Pad0.98x0.95mm_HandSolder
SW1: SW_DIP_x02; SW_DIP_SPSTx02_Piano_10.8x6.64mm_W7.62mm_P2.54mm
TP1, TP2, TP3: TestPoint; Pin_D1.0mm_L10.0mm
U1: MCP2562-E-P; DIP-8_W7.62mm
U2: MCP2515-I/P; DIP-18_W7.62mm; MPN MCP2515-I/P
U3: NJM7805SDL1; TO-252-2
U4: ADXL375
U5: TLP241B; DIP-4_W7.62mm
U6: ABX00012; ARDUINO_ABX00012; PARTREV 5
U7, U8: MB85RS2MT; DIP-8_W7.62mm
Y1: 8MHz; Crystal_SMD_HC49-SD

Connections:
+3.3V: C4.1, C5.1, C9.1, F1.1, R3.1, R16.1, U1.5 (Vio), U2.18 (VDD), U4.9 (VS), U4.10 (VDDI/O), U6.26 (+3V3)
+5V: C2.1, C7.1, C8.1, D2.2 (A), R2.1, U1.3 (VDD), U3.3 (OUT), U6.27 (VIN)
+12V: C3.1, D2.1 (K), J1.1, J1.2, U3.1 (IN)
CAN_H: J1.7, J1.8, R1.1, TP1.1, U1.7 (CANH)
CAN_L: J1.5, J1.6, R1.2, TP2.1, U1.6 (CANL)
CAN_RECEIVE_STATUS: R4.1, U6.9 (PA22_TC4-W0/0)
CAN_RX: U1.4 (RXD), U2.2 (RXCAN)
CAN_SEND_STATUS: R5.1, U6.10 (PA23_TC4-W1/1)
CAN_TX: U1.1 (TXD), U2.1 (TXCAN)
DEBUG_MODE: SW1.1, U6.6 (PA05_AIN5/A4)
DUMP_MODE: SW1.2, U6.5 (PA04_AIN4/A3)
GND: C1.1, C2.2, C3.2, C4.2, C5.2, C6.1, C7.2, C8.2, C9.2, D1.1 (K), D3.1 (K), D4.1 (K), D5.1 (K), D6.1 (K), D7.1 (K), D8.1 (K), D9.1 (K), J1.3, J1.4, J2.6 (VSS), J2.9 (DET_B), R8.2, SW1.3, SW1.4, U1.2 (VSS), U1.8 (STBY), U2.9 (VSS), U3.2 (GND), U4.1 (GND), U4.8 (GND), U5.2, U6.25 (GND), U7.4 (GND), U8.4 (GND)
LORA_RECEIVE_STATUS: R6.1, U6.4 (PB03_AIN11/A2)
LORA_SEND_STATUS: R7.1, U6.3 (PB02_AIN10/A1)
MEMORY_POWER: J2.4 (VDD), R9.1, R12.1, R13.1, R14.1, TP3.1, U5.4, U7.3 (~WP), U7.7 (~HOLD), U7.8 (VDD), U8.3 (~WP), U8.7 (~HOLD), U8.8 (VDD)
MEMORY_POWER_CONTROL: R10.1, U6.14 (PB11_TCC0-W5/~5)
unnamed: D1.2 (A), R2.2
unnamed: D3.2 (A), R4.2
unnamed: D4.2 (A), R5.2
unnamed: D5.2 (A), R6.2
unnamed: D6.2 (A), R7.2
unnamed: D7.2 (A), R11.2
unnamed: D8.2 (A), R15.2
unnamed: D9.2 (A), R9.2
unnamed: F1.2, U5.3
unnamed: R8.1, R10.2, U5.1
unnamed: R3.2, U2.17 (~RESET)
OSC1: C1.2, U2.8 (OSC1), Y1.2
OSC2: C6.2, U2.7 (OSC2), Y1.1
RECORD_STATUS: R11.1, U6.11 (PA10_TCC0-W2/~2)
SD_CHECK: J2.10 (DET_A), U6.12 (PA11_TCC0-W3/~3)
SD_STATUS: R15.1, U6.13 (PB10_TCC0-W4/~4)
SPI_CS_ADXL: R16.2, U4.5 (~CS), U6.2 (PA02_AIN0/DAC0/A0)
SPI_CS_FRAM0: R13.2, U6.8 (PA07_AIN7/A6), U8.1 (~CS)
SPI_CS_FRAM1: R14.2, U6.7 (PA06_AIN6/A5), U7.1 (~CS)
SPI_CS_MCP: U2.16 (~CS), U6.16 (PA21_TCC0-W7)
SPI_CS_SD: J2.2 (DAT3/CD), R12.2, U6.15 (PA20_TCC0-W6)
SPI_MISO: J2.7 (DAT0), U2.15 (SO), U4.4 (SDO/ALT_ADDRESS), U6.19 (PA19_S1_MISO), U7.2 (SO), U8.2 (SO)
SPI_MOSI: J2.3 (CMD), U2.14 (SI), U4.3 (SDA/SDI/SDIO), U6.17 (PA16_S1_MOSI), U7.5 (SI), U8.5 (SI)
SPI_SCLK: J2.5 (CLK), U2.13 (SCK), U4.2 (SCK/SCLK), U6.18 (PA17_S1_SCK), U7.6 (SCK), U8.6 (SCK)


Board: 2 copper layers, 110.0 x 95.0 mm, 50 parts (0 on the bottom side), 40 nets.

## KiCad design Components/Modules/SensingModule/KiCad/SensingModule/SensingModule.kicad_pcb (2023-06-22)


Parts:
C1, C2: 0.1uF; C_0603_1608Metric_Pad1.08x0.95mm_HandSolder
D1, D2: BLUE; LED_0603_1608Metric_Pad1.05x0.95mm_HandSolder
D3, D4: RED; LED_0603_1608Metric_Pad1.05x0.95mm_HandSolder
D5, D6: GREEN; LED_0603_1608Metric_Pad1.05x0.95mm_HandSolder
J1: Conn_01x08; Hirose_DF11B-8DP-2DS
R1, R3: 100R; R_0805_2012Metric_Pad1.20x1.40mm_HandSolder
R2: 120R; R_0603_1608Metric_Pad0.98x0.95mm_HandSolder
R4, R5: 10kR; R_0805_2012Metric_Pad1.20x1.40mm_HandSolder
R7: 2kR; R_0603_1608Metric_Pad0.98x0.95mm_HandSolder
R10, R11, R15: 300R; R_0603_1608Metric_Pad0.98x0.95mm_HandSolder
SW1: SW_DIP_x02; SW_DIP_SPSTx02_Piano_10.8x6.64mm_W7.62mm_P2.54mm
TP1, TP2: TestPoint; Pin_D1.0mm_L10.0mm
U1: MCP2562-E-P; DIP-8_W7.62mm
U5: NUCLEO-F303K8; MODULE_NUCLEO-F303K8; PARTREV 5

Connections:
+3.3V: C2.1, R4.1, R5.1, U1.5 (Vio), U5.4_14 (+3V3); also elsewhere on the board
+5V: C1.1, U1.3 (VDD), U5.4_4 (+5V)
+12V: J1.1, J1.2, R7.1, U5.4_1 (VIN)
CAN_H: J1.7, J1.8, R2.1, TP1.1, U1.7 (CANH)
CAN_L: J1.5, J1.6, R2.2, TP2.1, U1.6 (CANL)
CAN_RECEIVE_STATUS: R1.1, U5.3_14 (PB5)
CAN_RX: U1.4 (RXD), U5.3_13 (PA11)
CAN_SEND_STATUS: R3.1, U5.3_15 (PB4)
CAN_TX: U1.1 (TXD), U5.3_5 (PA12)
DEBUG_MODE: SW1.1, U5.3_6 (PB0)
DUMP_MODE: SW1.2, U5.4_5 (PA2)
GND: C1.2, C2.2, D1.1 (K), D2.1 (K), D3.1 (K), D4.1 (K), D5.1 (K), D6.1 (K), J1.3, J1.4, SW1.3, SW1.4, U1.2 (VSS), U1.8 (STBY), U5.3_4 (GND_1), U5.4_2 (GND_2); also elsewhere on the board
I2C_SCL: R5.2, U5.3_8 (PB6); also elsewhere on the board
I2C_SDA: R4.2, U5.3_7 (PB7); also elsewhere on the board
unnamed: D1.2 (A), R1.2
unnamed: D2.2 (A), R3.2
unnamed: D3.2 (A), R7.2
unnamed: D4.2 (A), R10.2
unnamed: D5.2 (A), R11.2
unnamed: D6.2 (A), R15.2
RECORDER_POWER: R10.1; also elsewhere on the board
RECORDER_POWER_CONTROL: U5.3_10 (PF0); also elsewhere on the board
RECORD_STATUS: R11.1, U5.3_9 (PB1)
SD_CHECK: U5.3_11 (PF1); also elsewhere on the board
SD_STATUS: R15.1, U5.3_12 (PA8)
SPI_CS_FRAM0: U5.4_10 (PA3); also elsewhere on the board
SPI_CS_FRAM1: U5.4_9 (PA4); also elsewhere on the board
SPI_CS_SD: U5.4_12 (PA0); also elsewhere on the board
SPI_MISO: U5.4_7 (PA6); also elsewhere on the board
SPI_MOSI: U5.4_6 (PA7); also elsewhere on the board
SPI_SCLK: U5.4_8 (PA5); also elsewhere on the board
THERMISTOR: U5.4_11 (PA1); also elsewhere on the board


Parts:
C3: 47uF; CP_Elec_6.3x5.9
F1: Polyfuse; Fuse_1206_3216Metric_Pad1.42x1.75mm_HandSolder
J4: Micro_SD_Card_Det_Hirose_DM3AT; microSD_HC_Hirose_DM3AT-SF-PEJM5
R6, R8: 120R; R_0603_1608Metric_Pad0.98x0.95mm_HandSolder
R12, R13, R14: 4.7kR; R_0603_1608Metric_Pad0.98x0.95mm_HandSolder
TP3: TestPoint; Pin_D1.0mm_L10.0mm
U4: TLP241B; DIP-4_W7.62mm
U6, U7: MB85RS2MT; DIP-8_W7.62mm

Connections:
+3.3V: C3.1, F1.1; also elsewhere on the board
GND: C3.2, J4.6 (VSS), J4.9 (DET_B), R6.2, U4.2, U6.4 (GND), U7.4 (GND); also elsewhere on the board
unnamed: F1.2, U4.3
unnamed: R6.1, R8.2, U4.1
RECORDER_POWER: J4.4 (VDD), R12.1, R13.1, R14.1, TP3.1, U4.4, U6.3 (~WP), U6.7 (~HOLD), U6.8 (VDD), U7.3 (~WP), U7.7 (~HOLD), U7.8 (VDD); also elsewhere on the board
RECORDER_POWER_CONTROL: R8.1; also elsewhere on the board
SD_CHECK: J4.10 (DET_A); also elsewhere on the board
SPI_CS_FRAM0: R12.2, U6.1 (~CS); also elsewhere on the board
SPI_CS_FRAM1: R13.2, U7.1 (~CS); also elsewhere on the board
SPI_CS_SD: J4.2 (DAT3/CD), R14.2; also elsewhere on the board
SPI_MISO: J4.7 (DAT0), U6.2 (SO), U7.2 (SO); also elsewhere on the board
SPI_MOSI: J4.3 (CMD), U6.5 (SI), U7.5 (SI); also elsewhere on the board
SPI_SCLK: J4.5 (CLK), U6.6 (SCK), U7.6 (SCK); also elsewhere on the board


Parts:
J2: Conn_01x02_Pin; Hirose_DF1B
R9: 10kR; R_0805_2012Metric_Pad1.20x1.40mm_HandSolder
U2: BME280
U3: BNO055

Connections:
+3.3V: R9.1, U2.1 (VDD), U2.3 (SCB), U3.1 (VIN); also elsewhere on the board
GND: J2.1, U2.2 (GND), U2.5 (SDO), U3.7 (GND); also elsewhere on the board
I2C_SCL: U2.6 (SCK), U3.4 (SCL/R); also elsewhere on the board
I2C_SDA: U2.4 (SDI), U3.3 (SDA/T); also elsewhere on the board
THERMISTOR: J2.2, R9.2; also elsewhere on the board


Board: 2 copper layers, 110.0 x 95.0 mm, 39 parts (0 on the bottom side), 34 nets.

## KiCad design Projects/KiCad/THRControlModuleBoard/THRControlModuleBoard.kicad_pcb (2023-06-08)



Board: 2 copper layers, 87.2 x 130.0 mm, 67 parts (33 on the bottom side), 58 nets.

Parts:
A1: Arduino_Nano_Every; Arduino_Nano
C1, C3: 0.01uF; C_0603_1608Metric_Pad1.08x0.95mm_HandSolder
C2, C4, C5, C6, C7, C8, C9, C12, C13, C14, C15, C16, C17: 0.1uF; C_0603_1608Metric_Pad1.08x0.95mm_HandSolder
C10, C11: 15pF; C_0603_1608Metric_Pad1.08x0.95mm_HandSolder
D1, D2, D3: D; D_SOD-123
D4, D5: MM3Zxx; D_SOD-323F
D6: LED; LED_0603_1608Metric_Pad1.05x0.95mm_HandSolder
D7: 1N4148W; D_SOD-123
H1, H2, H3, H4: MountingHole; MountingHole_4.5mm
IC1, IC2: LTC1480CN8#PBF; DIP794W53P254L1016H394Q8N
J1: Screw_Terminal_01x02; RS_PRO_611-8157
J2, J3: Conn_02x03_Odd_Even; Hirose_DF51A-6DP-2DSA
J4, J5: Conn_01x04; CONNECTOR_4-STRAIGHT
J6: Conn_02x04_Odd_Even; Hirose_DF11B-8DP-2DS
JP1, JP2: SolderJumper_2_Bridged; SolderJumper-2_P1.3mm_Open_TrianglePad1.0x1.5mm
LS1: PKB24SPCH3601-B0; SPKR_PKB24SPCH3601-B0
R1, R2: 100; R_0805_2012Metric_Pad1.20x1.40mm_HandSolder
R3, R4, R5, R9, R12, R14, R15, R16, R17, R18: 10k; R_0603_1608Metric_Pad0.98x0.95mm_HandSolder
R6, R7, R8: 120; R_0603_1608Metric_Pad0.98x0.95mm_HandSolder
R13, R19, R20, R21, R22, R23, R24: 1k; R_0603_1608Metric_Pad0.98x0.95mm_HandSolder
U1: MAX31856MUD+T; TSSOP-14_4.4x5mm_P0.65mm
U2: Value: Value: Value: Value: MCP2562-E-P; DIP-8_W7.62mm
U3: MCP2515-I/P; DIP254P762X432-18
U5: MAX31855
Y1: 8MHz; Crystal_HC49-4H_Vertical

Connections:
+3.3V: A1.17 (3V3), C4.1, C5.1, C7.1, C8.1, C9.1, IC1.8 (VCC), IC2.8 (VCC), R3.1, R4.1, R5.1, R9.1, U1.5 (AVDD), U1.8 (DVDD), U3.18 (VDD), U5.1 (Vin)
+5V: A1.27 (+5V), C6.2, U2.3 (VDD), U2.5 (Vio)
+12V: A1.30 (VIN), D4.1 (K), D5.1 (K), D7.1 (K), J4.2, J5.2
+VDC: J2.6, J3.4
B3M_Servo__Close: A1.20 (A1), R22.2
B3M_Servo__Closeinput: J6.8, R17.1
B3M_Servo__Open: A1.19 (A0), R21.2
B3M_Servo__Openinput: J6.6, R16.1
BIAS: J1.1, R2.1, U1.2 (BIAS)
CAN__H: J3.6, R6.1, U2.7 (CANH)
CAN__L: J3.5, R6.2, U2.6 (CANL)
CAN__RXD-CANRX: U2.4 (RXD), U3.2 (RXCAN)
CAN__TXD-TXCAN: U2.1 (TXD), U3.1 (TXCAN)
DRDY: JP1.1 (A), U1.7 (~DRDY)
GND: A1.4 (GND), A1.29 (GND), C1.1, C3.2, C4.2, C5.2, C6.1, C7.2, C8.2, C9.2, C10.2, C11.2, C12.2, C13.2, C14.2, C15.2, C16.2, C17.2, D4.2 (A), D5.2 (A), D6.1 (K), IC1.5 (GND), IC2.5 (GND), J2.1, J2.3, J2.5, J3.1, J3.3, J4.1, J5.1, J6.1, J6.3, J6.5, J6.7, LS1.N, U1.1 (AGND), U1.14 (DGND), U2.2 (VSS), U2.8 (STBY), U3.9 (VSS), U5.3 (GND)
IO__Busser: A1.25 (A6), LS1.P
MAX31855__~CS-~CS: A1.8 (D5), U5.5 (~CS)
MAX31856__DRDY-DRDY: A1.12 (D9), JP1.2 (B)
MAX31856__FAULT-FAULT: A1.13 (D10), JP2.2 (B)
MAX31856__~CS-~CS: A1.7 (D4), D3.1 (K)
MCP2515__~CS-~CS: A1.9 (D6), U3.16 (~CS)
unnamed: C12.1, R12.2, R13.1
unnamed: C13.1, R14.2, R19.1
unnamed: C14.1, R15.2, R20.1
unnamed: C15.1, R16.2, R21.1
unnamed: C16.1, R17.2, R22.1
unnamed: C17.1, R18.2, R23.1
unnamed: D1.2 (A), R3.2, U1.12 (SDI)
unnamed: D2.2 (A), R4.2, U1.10 (SCK)
unnamed: D3.2 (A), R5.2, U1.9 (~CS)
unnamed: D6.2 (A), R24.2
unnamed: D7.2 (A), J3.2, R24.1
unnamed: J1.2, R1.1
unnamed: C1.2, C2.1, R1.2, U1.4 (T+)
unnamed: C2.2, C3.1, R2.2, U1.3 (T-)
unnamed: R9.2, U3.17 (~RESET)
OCS1: C10.1, U3.8 (OSC1), Y1.2
OCS2: C11.1, U3.7 (OSC2), Y1.1
RS405_Servo__Close: A1.22 (A3), R23.2
RS405_Servo__Closeinput: J6.4, R18.1
RS405_Servo__Open: A1.21 (A2), R13.2
RS405_Servo__Openinput: J6.2, R12.1
RS485__A1: IC1.6 (A), J4.3, R7.2
RS485__A2: IC2.6 (A), J5.3, R8.2
RS485__B1: IC1.7 (B), J4.4, R7.1
RS485__B2: IC2.7 (B), J5.4, R8.1
RS485__DI-TX: A1.1 (TX1), IC1.4 (DI), IC2.4 (DI)
RS485__ENABLE_B3M: A1.5 (D2), IC1.2 (~RE), IC1.3 (DE)
RS485__ENABLE_RS405: A1.6 (D3), IC2.2 (~RE), IC2.3 (DE)
RS485__RO-RX: A1.2 (RX1), IC1.1 (RO), IC2.1 (RO)
SPI__MISO: A1.15 (MISO), U1.11 (SDO), U3.15 (SO), U5.4 (DO)
SPI__MOSI: A1.14 (MOSI), D1.1 (K), U3.14 (SI)
SPI__SCLK: A1.16 (SCK), D2.1 (K), U3.13 (SCK), U5.6 (SCK)
Umbilical__launchInput: J2.4, R14.1
Umbilical__launchPin: A1.10 (D7), R19.2
Umbilical__waitingInput: J2.2, R15.1
Umbilical__waitingPin: A1.11 (D8), R20.2
~FAULT: JP2.1 (A), U1.13 (~FAULT)

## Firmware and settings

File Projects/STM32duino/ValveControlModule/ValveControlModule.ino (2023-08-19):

#include <TaskManager.h>
#include "IcsHardSerialClass.h"
#include <SPI.h>
#include <mcp2515_can.h>

/* CAN Config START */
const uint8_t SPI_CS_PIN = 6;
mcp2515_can CAN(SPI_CS_PIN);
/* CAN Config END */

/* CANDATA Config START */
namespace StateTransition
{
    enum class Mode : uint8_t
    {
        LAUNCH,
        WAITING,
    };

    Mode ChangeMode;
}

namespace Error
{
    enum class ErrorCode : uint8_t
    {
        MOTOR_POSITION_FAILED,
    };

    ErrorCode ErrorCode;
}

union Converter
{
    uint8_t data[6];
    int16_t data_16[3];
} converter;

/* CANDATA Config END */

/* B3M Servo Config START */
const byte ENABLE_PIN = 2;
const long BAUNDRATE = 115200;
const int TIMEOUT = 500;
IcsHardSerialClass B3M(&Serial1, ENABLE_PIN, BAUNDRATE, TIMEOUT);
/* B3M Servo Config END */

/* RS405CB Servo Config START */
uint8_t REDE_PIN = 3;
int rs405cbCloseangle = -800;
int rs405cbOpenangle = 0;
/* RS405CB Servo Config END */

/* State Transition Config START */
constexpr uint8_t POSITION_CHANGING_THRESHOLD = 5;
uint8_t WaitingCount = 0;
uint8_t LaunchCount = 0;
uint8_t Position = 1;
uint8_t WaitingPin = 7;
uint8_t LaunchPin = 8;
/* State Transition Config END */

/* Buzzer Config START */
const uint8_t BuzzerPin = A6;
/* Buzzer Config END */

/* LED Config START */
const uint8_t LaunchLED = A2;
const uint8_t WaitingLED = A3;
const uint8_t TasksLED = A7;
/* LED Config END */

uint32_t torqueTime;

void setup()
{
    Serial1.begin(115200);
    Serial1.begin(115200, SERIAL_8N1);

    Serial.begin(115200);


    pinMode(REDE_PIN, OUTPUT);
    Torque(0x01, 0x01);
    Move(1, rs405cbOpenangle, 100);

    SignalInitialize();
    StateTransition::ChangeMode = StateTransition::Mode::WAITING;

    B3M.begin();
    B3M_initialize();
    B3M_setposition(0x01, 0, 1000);

    CAN.begin(CAN_1000KBPS, MCP_8MHz); // CAN_1000Kbps, MCP_8MHzに設定

    // デバック用
    //  while (CAN_OK != CAN.begin(CAN_250KBPS, MCP_8MHz))
    //  {
    //      Serial.println("CAN init fail, retry...");
    //      delay(100);
    //  }
    //  Serial.println("CAN init ok!");

    BuzzerInitialize();
    LEDInitialize();

    Tasks.add("CAN", []()
        {
            ToggleTasksLED();
            Serial.print(" |Error-Sta|> ");
            Serial.print(b3mReaderrorStatus(0x01));
            Serial.print(" |System-Error-Sta|> ");
            Serial.print(b3mReadsystemError(0x01));
            Serial.print(" |Motor-Sta|> ");
            Serial.print(b3mReadmotorStatus(0x01));
            Serial.print(" |Uart-Rece-Error|> ");
            Serial.print(b3mReaduartReceptionerror(0x01));
            Serial.print(" |Command-Error|> ");
            Serial.println(b3mReadcommandError(0x01));

            uint32_t currentTime = millis();

            //   147~149の処理で特に問題が無ければ削除
            int16_t recieveCurrentposition = b3mReadcurrentPosition(0x01);
            int16_t recieveDesiredPosition = b3mReaddesiredPosition(0x01);
            int16_t recieveCurrentvelosity = b3mReadcurrentVelosity(0x01);
            uint8_t recieveCurrent = b3mReadcurrent(0x01);
            uint8_t recieveMcutemperature = b3mReadmcuTemperature(0x01);
            uint8_t recieveMotortemperature = b3mReadmotorTemperature(0x01);
            uint8_t recieveinputVoltage = b3mreadInputvoltage(0x01);
            // uint8_t recieveStatus = b3mreadStatus(0x01);

          //   Serial.print(recieveCurrentposition);
          //   Serial.print(" <| ");
          //   Serial.print(recieveDesiredPosition);
          //   Serial.print(" <| ");
          //   Serial.print(recieveCurrentvelosity);
          //   Serial.print(" <| ");
          //   Serial.print(recieveStatus);
          //   Serial.print(" <| ");
          //   Serial.print(recieveMotortemperature);
          //   Serial.print(" <| ");
          //   Serial.print(recieveMcutemperature);
          //   Serial.print(" <| ");
          // Serial.print(b3mReadcurrent(0x01));
          // Serial.print(" <| ");
          //   Serial.print(recieveinputVoltage);
          //   Serial.print(" <| ");

            canSendmcuInfomation(recieveMotortemperature, recieveMcutemperature, recieveCurrent, recieveinputVoltage);
            canSendmotorInfomation(recieveCurrentposition, recieveDesiredPosition, recieveCurrentvelosity);
            //   canSendmcuInfomation(b3mReadmotorTemperature(0x01), b3mReadmcuTemperature(0x01), b3mReadcurrent(0x01), b3mreadInputvoltage(0x01));
            //   canSendmotorInfomation(b3mReadcurrentPosition(0x01), b3mReaddesiredPosition(0x01), b3mReadcurrentVelosity(0x01)); 
            //   canSendservoStatusinfomation(b3mReaderrorStatus(0x01), b3mReadsystemError(0x01), b3mReadmotorStatus(0x01), b3mReaduartReceptionerror(0x01), b3mReadcommandError(0x01));
            canSendmotorStatus(b3mReadmotorStatus(0x01), currentTime); })
        ->startFps(13);

            // Tasks.add("Count", []()
            //           {
            //             Serial.print(F("Mode: "));
            //             if (StateTransition::ChangeMode == StateTransition::Mode::LAUNCH)
            //             {
            //                 Serial.print(F("LAUNCH"));
            //                 Serial.print(F(" | "));
            //             }
            //             else
            //             {
            //                 Serial.print(F("WAITING"));
            //                 Serial.print(F(" | "));

            //             };
            //             Serial.print(F("launchCount: "));
            //             Serial.print(LaunchCount);
            //             Serial.print(F(" | "));
            //             Serial.print(F("waitingCount: "));
            //             Serial.print(WaitingCount);
            //             Serial.print(F(" | "));
            //             Serial.println(""); })
            // ->startFps(100);

            Tasks.add("Mode", []()
                {
                    uint8_t can[1];
                    can[0] = static_cast<uint8_t>(StateTransition::ChangeMode);
                    CAN.sendMsgBuf(0x10A, 0, 1, can);
                    // Serial.print(can[0]);
                    // Serial.println(" | ");
                })
                ->startFps(59);

                Tasks.add("TorqueOff", []()
                    {
                        TorqueOff();
                    });

                Tasks.add("B3Mon", []() {
                    B3M_setposition(0x01, -5500, 100);
                    });

                Tasks.add("B3Moff", []() {
                    B3M_setposition(0x01, 0, 2000);
                    });

                Tasks.add("Buzzer", []()
                    { ToggleBuzzer(); });

                /* Wake Up Buzzer */
                Tasks["Buzzer"]->startIntervalMsecForCount(66, 10);
}

void loop()
{
    Tasks.update();

    if (Position == 1 && digitalRead(LaunchPin) == LOW)
    {
        // TorqueTime = millis();
        Tasks["TorqueOff"]->startOnceAfterSec(3);
        Tasks["B3Mon"]->startOnceAfterMsec(800);
        Torque(0x01, 0x01);
        ChangeLaunchMode();
    }

    if (Position == 2 && digitalRead(WaitingPin) == LOW)
    {
        Tasks["TorqueOff"]->startOnceAfterSec(3);
        Tasks["B3Moff"]->startOnceAfterSec(1);
        Torque(0x01, 0x01);
        ChangeWaitingMode();
    }
}

void canSendmode()
{
    uint8_t can[1];
    can[0] = static_cast<uint8_t>(StateTransition::ChangeMode);
    CAN.sendMsgBuf(0x10A, 0, 1, can);
    Serial.print(can[0]);
}

void Torque(unsigned char ID, unsigned char data)
{
    unsigned char TxData[9];
    unsigned char CheckSum = 0;

    // パケットデータ生成
    TxData[0] = 0xFA; // HEADER
    TxData[1] = 0xAF; // HEADER
    TxData[2] = ID;   // ID
    TxData[3] = 0x00; // FLAGS
    TxData[4] = 0x24; // ADDRESS
    TxData[5] = 0x01; // LENGTH
    TxData[6] = 0x01; // COUNT
    TxData[7] = data; // DATA

    for (int i = 2; i <= 7; i++)
    {
        CheckSum = CheckSum ^ TxData[i];
    }

    TxData[8] = CheckSum;

    digitalWrite(REDE_PIN, HIGH);
    for (int i = 0; i <= 8; i++)
    {
        Serial1.write(TxData[i]);
    }

    Serial1.flush();
    digitalWrite(REDE_PIN, LOW);
}

void Move(unsigned char ID, int Angle, int Speed)
{
    unsigned char TxData[12];
    unsigned char CheckSum = 0;

    // パケットデータ生成
    TxData[0] = 0xFA; // HEADER
    TxData[1] = 0xAF; // HEADER
    TxData[2] = ID;   // ID
    TxData[3] = 0x00; // FLAGS
    TxData[4] = 0x1E; // ADDRESS
    TxData[5] = 0x04; // LENGTH
    TxData[6] = 0x01; // COUNT
    // Angle
    TxData[7] = (unsigned char)0x00FF & Angle;
    TxData[8] = (unsigned char)0x00FF & (Angle >> 8);
    // Speed
    TxData[9] = (unsigned char)0x00FF & Speed;
    TxData[10] = (unsigned char)0x00FF & (Speed >> 8);
    // チェックサム計算
    for (int i = 2; i <= 10; i++)
    {
        CheckSum = CheckSum ^ TxData[i];
    }
    TxData[11] = CheckSum;

    // パケットデータ送信
    digitalWrite(REDE_PIN, HIGH);
    for (int i = 0; i <= 11; i++)
    {
        Serial1.write(TxData[i]);
    }
    Serial1.flush();

    digitalWrite(REDE_PIN, LOW);
}

int B3M_writeCommand(byte id, byte TxData, byte Address)
{
    byte txCmd[8];
    byte rxCmd[5];
    unsigned int reData;
    bool flag;

    txCmd[0] = (byte)(0x08); // SIZE      //一連コマンドのバイト数。今回は8バイト
    txCmd[1] = (byte)(0x04); // COMMAND   //何をするための処理か設定。 0x04はWrite
    txCmd[2] = (byte)(0x00); // OPTION    //ステータスの読み取り。 0x00はERROR STATUS
    txCmd[3] = (byte)(id);   // ID        //制御するサーボID番号を指定

    txCmd[4] = (byte)(TxData);  // DATA      //
    txCmd[5] = (byte)(Address); // ADDRESS   //

    txCmd[6] = (byte)(0x01); // COUNT
    txCmd[7] = (byte)(0x00); // 初期化

    // Serial.print("tx: ");
    for (int i = 0; i < 7; i++)
    {
        txCmd[7] += txCmd[i];
        // Serial.print(txCmd[i]);
        // Serial.print("|");
    }
    // Serial.println("");
    txCmd[7] = (byte)(txCmd[7]); // CHECKSUM

    // flag = B3M.synchronize(txCmd, sizeof txCmd, rxCmd, sizeof rxCmd);
    flag = B3M.synchronize(txCmd, 8, rxCmd, 5);

    if (flag == false)
    {
        return -1;
        Serial.println(F("synchronize ERROR"));
    }

    // Serial.print("rx: ");
    for (int o = 0; o < 7; o++)
    {
        rxCmd[7] += rxCmd[o];
        // Serial.print(rxCmd[o]);
        // Serial.print("|");
    }
    // Serial.println("");

    reData = rxCmd[2];
    return reData;
}

int B3M_setposition(byte id, int Pos, int Time)
{
    byte txCmd[9];
    byte rxCmd[7];
    unsigned int reData;
    bool flag;

    txCmd[0] = (byte)(0x09); // SIZE
    txCmd[1] = (byte)(0x06); // COMMAND //0x06はポジションを変更する
    txCmd[2] = (byte)(0x00); // OPTION
    txCmd[3] = (byte)(id);   // ID

    txCmd[4] = (byte)(Pos & 0xFF);      // POS_L
    txCmd[5] = (byte)(Pos >> 8 & 0xFF); // POS_H

    txCmd[6] = (byte)(Time & 0xFF);      // TIME_L
    txCmd[7] = (byte)(Time >> 8 & 0xFF); // TIME_H

    txCmd[8] = 0x00;

    // Serial.print("tx: ");
    for (int i = 0; i < 8; i++)
    {
        txCmd[8] += txCmd[i];
        // Serial.print(txCmd[i]);
        // Serial.print("|");
    }
    // Serial.println("|");
    txCmd[8] = (byte)(txCmd[8]); // SUM

    // flag = B3M.synchronize(txCmd, sizeof txCmd, rxCmd, sizeof rxCmd);
    flag = B3M.synchronize(txCmd, 9, rxCmd, 7);

    if (flag == false)
    {
        return -1;
        Serial.println(F("synchronize ERROR"));
    }

    // Serial.print("rx: ");
    for (int o = 0; o < 7; o++)
    {
        // Serial.print(rxCmd[o]);
        // Serial.print("|");
    }
    // Serial.println("");

    reData = rxCmd[7];
    return reData;
}

void B3M_initialize()
{
    B3M_writeCommand(0x01, 0x02, 0x28); // 動作モード：Free
    // Serial.println(B3M_writeCommand(0x01, 0x02, 0x28));

    B3M_writeCommand(0x01, 0x02, 0x28); // 位置制御モードに設定
    // Serial.println(B3M_writeCommand(0x01, 0x02, 0x28));

    B3M_writeCommand(0x01, 0x01, 0x29); // 起動生成タイプ：Even
    // Serial.println(B3M_writeCommand(0x01, 0x01, 0x29));

    B3M_writeCommand(0x01, 0x00, 0x5c); // ゲインプリセット：No.0
    // Serial.println(B3M_writeCommand(0x01, 0x00, 0x5c));

    B3M_writeCommand(0x01, 0x00, 0x28); // 動作モード：Normal
    // Serial.println(B3M_writeCommand(0x01, 0x00, 0x28));
}

void ChangeLaunchMode()
{
    if (Position == 1 && digitalRead(LaunchPin) == LOW)
    {
        LaunchCount++;
    }
    else
    {
        LaunchCount = 0;
    }

    if (LaunchCount >= POSITION_CHANGING_THRESHOLD)
    {
        // torqueTime = millis();
        StateTransition::ChangeMode = StateTransition::Mode::LAUNCH;

        Move(1, -800, 80); //-800/10 = -80deg
        // delay(500);
        // B3M_setposition(0x01, -5500, 100); //-5500/100 = -55deg
        Tasks["Buzzer"]->startIntervalMsecForCount(50, 6);

        LaunchCount = 0;
        Position = 2;

        digitalWrite(LaunchLED, HIGH);
        digitalWrite(WaitingLED, LOW);

        // if (millis() - torqueTime >= 5000)
        // {
        //     Torque(0x01, 0x00);
        //     Serial.print("Hello");
        // }
    }
}

void TorqueOff()
{
    Torque(0x01, 0x00);
}

void ChangeWaitingMode()
{
    if (Position == 2 && digitalRead(WaitingPin) == LOW)
    {
        WaitingCount++;
    }
    else
    {
        WaitingCount = 0;
    }

    if (WaitingCount >= POSITION_CHANGING_THRESHOLD)
    {
        // torqueTime = millis();
        StateTransition::ChangeMode = StateTransition::Mode::WAITING;

        Move(1, 0, 200);
        // delay(500);
        B3M_setposition(0x01, 0, 2000);
        Tasks["Buzzer"]->startIntervalMsecForCount(100, 4);

        WaitingCount = 0;
        Position = 1;

        digitalWrite(WaitingLED, HIGH);
        digitalWrite(LaunchLED, LOW);

        // uint32_t nowTime = millis();
        // if (nowTime - torqueTime >= 5000)
        // {
        //     Torque(0x01, 0x00);
        //     Serial.print("Arduino");
        // }
        // torqueTime = nowTime;
    }
}

void SignalInitialize()
{
    pinMode(LaunchPin, INPUT_PULLUP);
    pinMode(WaitingPin, INPUT_PULLUP);
}

void BuzzerInitialize()
{
    pinMode(BuzzerPin, OUTPUT);
}

void LEDInitialize()
{
    pinMode(WaitingLED, OUTPUT);
    pinMode(LaunchLED, OUTPUT);
    pinMode(TasksLED, OUTPUT);

    digitalWrite(LaunchLED, LOW);
    digitalWrite(WaitingLED, HIGH);
}

void ToggleTasksLED()
{
    digitalWrite(TasksLED, !digitalRead(TasksLED));
}

void ToggleBuzzer()
{
    digitalWrite(BuzzerPin, !digitalRead(BuzzerPin));
}

int16_t b3mReaddesiredPosition(byte id)
{
    byte txCmd[7];
    byte rxCmd[7];
    int16_t value;
    int16_t reData;
    bool flag;

    txCmd[0] = (byte)(0x07); // SIZE
    txCmd[1] = (byte)(0x03); // COMMAND
    txCmd[2] = (byte)(0x00); // OPTION
    txCmd[3] = (byte)(id);   // ID

    txCmd[4] = (byte)(0x2A); // ADDRESS //目標位置のアドレス
    txCmd[5] = (byte)(0x02); // LENGTH

    txCmd[6] = 0x00; // SUM

    for (int i = 0; i < 6; i++)
    {
        txCmd[6] += txCmd[i];
        // Serial.print(txCmd[i]);
        // Serial.print("|");
    }
    // Serial.println("");

    txCmd[6] = (byte)(txCmd[6]);
    flag = B3M.synchronize(txCmd, 7, rxCmd, 7);

    if (flag == false)
    {
        return -1;
    }

    // Serial.print("RAM: ");
    for (int o = 4; o < 6; o++)
    {
        value = (rxCmd[o] << 8) | rxCmd[o];
        // Serial.print(rxCmd[o], HEX);
        // Serial.print(" ");
    }
    // Serial.print(" | ");

    reData = (value & 0xFF) << 8 | (value >> 8 & 0xFF);

    return reData / 100;
}

int16_t b3mReadcurrentPosition(byte id)
{
    byte txCmd[7];
    byte rxCmd[7];
    int16_t value;
    int16_t reData;
    bool flag;

    txCmd[0] = (byte)(0x07); // SIZE
    txCmd[1] = (byte)(0x03); // COMMAND
    txCmd[2] = (byte)(0x00); // OPTION
    txCmd[3] = (byte)(id);   // ID

    txCmd[4] = (byte)(0x2C); // ADDRESS  //現在位置のアドレス
    txCmd[5] = (byte)(0x02); // LENGTH

    txCmd[6] = 0x00; // SUM

    for (int i = 0; i < 6; i++)
    {
        txCmd[6] += txCmd[i];
        // Serial.print(txCmd[i]);
        // Serial.print("|");
    }
    // Serial.println("");

    txCmd[6] = (byte)(txCmd[6]);
    flag = B3M.synchronize(txCmd, 7, rxCmd, 7);

    if (flag == false)
    {
        return -1;
    }

    // Serial.print("RAM: ");
    for (int o = 4; o < 6; o++)
    {
        value = (rxCmd[o] << 8) | rxCmd[o];
        // Serial.print(rxCmd[o], HEX);
        // Serial.print(" ");
    }
    // Serial.print(" | ");

    reData = (value & 0xFF) << 8 | (value >> 8 & 0xFF);

    return reData / 100;
}

int16_t b3mReadcurrentVelosity(byte id)
{
    byte txCmd[7];
    byte rxCmd[7];
    int16_t value;
    int16_t reData;
    bool flag;

    txCmd[0] = (byte)(0x07); // SIZE
    txCmd[1] = (byte)(0x03); // COMMAND
    txCmd[2] = (byte)(0x00); // OPTION
    txCmd[3] = (byte)(id);   // ID

    txCmd[4] = (byte)(0x32); // ADDRESS  //現在速度のアドレス
    txCmd[5] = (byte)(0x02); // LENGTH

    txCmd[6] = 0x00; // SUM

    for (int i = 0; i < 6; i++)
    {
        txCmd[6] += txCmd[i];
        // Serial.print(txCmd[i]);
        // Serial.print("|");
    }
    // Serial.println("");

    txCmd[6] = (byte)(txCmd[6]);
    flag = B3M.synchronize(txCmd, 7, rxCmd, 7);

    if (flag == false)
    {
        return -1;
    }

    // Serial.print("RAM: ");
    for (int o = 4; o < 6; o++)
    {
        value = (rxCmd[o] << 8) | rxCmd[o];
        // Serial.print(rxCmd[o], HEX);
        // Serial.print(" ");
    }
    // Serial.print(" | ");

    reData = (value & 0xFF) << 8 | (value >> 8 & 0xFF);

    return reData / 100;
}

int16_t b3mReadmcuTemperature(byte id)
{
    byte txCmd[7];
    byte rxCmd[7];
    int16_t value;
    int16_t reData;
    bool flag;

    txCmd[0] = (byte)(0x07); // SIZE
    txCmd[1] = (byte)(0x03); // COMMAND
    txCmd[2] = (byte)(0x00); // OPTION
    txCmd[3] = (byte)(id);   // ID

    txCmd[4] = (byte)(0x44); // ADDRESS  //現在のMCU温度のアドレス
    txCmd[5] = (byte)(0x02); // LENGTH

    txCmd[6] = 0x00; // SUM

    for (int i = 0; i < 6; i++)
    {
        txCmd[6] += txCmd[i];
        // Serial.print(txCmd[i]);
        // Serial.print("|");
    }
    // Serial.println("");

    txCmd[6] = (byte)(txCmd[6]);
    flag = B3M.synchronize(txCmd, 7, rxCmd, 7);

    if (flag == false)
    {
        return -1;
    }

    // Serial.print("RAM: ");
    for (int o = 4; o < 6; o++)
    {
        value = (rxCmd[o] << 8) | rxCmd[o];
        // Serial.print(rxCmd[o], HEX);
        // Serial.print(" ");
    }
    // Serial.print(" | ");

    reData = (value & 0xFF) << 8 | (value >> 8 & 0xFF);

    return reData / 100;
}

int16_t b3mReadmotorTemperature(byte id)
{
    byte txCmd[7];
    byte rxCmd[7];
    int16_t value;
    int16_t reData;
    bool flag;

    txCmd[0] = (byte)(0x07); // SIZE
    txCmd[1] = (byte)(0x03); // COMMAND
    txCmd[2] = (byte)(0x00); // OPTION
    txCmd[3] = (byte)(id);   // ID

    txCmd[4] = (byte)(0x46); // ADDRESS  //現在のモーター温度のアドレス
    txCmd[5] = (byte)(0x02); // LENGTH

    txCmd[6] = 0x00; // SUM

    for (int i = 0; i < 6; i++)
    {
        txCmd[6] += txCmd[i];
        // Serial.print(txCmd[i]);
        // Serial.print("|");
    }
    // Serial.println("");

    txCmd[6] = (byte)(txCmd[6]);
    flag = B3M.synchronize(txCmd, 7, rxCmd, 7);

    if (flag == false)
    {
        return -1;
    }

    // Serial.print("RAM: ");
    for (int o = 4; o < 6; o++)
    {
        value = (rxCmd[o] << 8) | rxCmd[o];
        // Serial.print(rxCmd[o], HEX);
        // Serial.print(" ");
    }
    // Serial.print(" | ");

    reData = (value & 0xFF) << 8 | (value >> 8 & 0xFF);

    return reData / 100;
}

int16_t b3mReadcurrent(byte id)
{
    byte txCmd[7];
    byte rxCmd[7];
    int16_t value;
    int16_t reData;
    bool flag;

    txCmd[0] = (byte)(0x07); // SIZE
    txCmd[1] = (byte)(0x03); // COMMAND
    txCmd[2] = (byte)(0x00); // OPTION
    txCmd[3] = (byte)(id);   // ID

    txCmd[4] = (byte)(0x48); // ADDRESS  //現在負荷電流値のアドレス
    txCmd[5] = (byte)(0x02); // LENGTH

    txCmd[6] = 0x00; // SUM

    for (int i = 0; i < 6; i++)
    {
        txCmd[6] += txCmd[i];
        // Serial.print(txCmd[i]);
        // Serial.print("|");
    }
    // Serial.println("");

    txCmd[6] = (byte)(txCmd[6]);
    flag = B3M.synchronize(txCmd, 7, rxCmd, 7);

    if (flag == false)
    {
        return -1;
    }

    // Serial.print("RAM: ");
    for (int o = 4; o < 6; o++)
    {
        value = (rxCmd[o] << 8) | rxCmd[o];
        // Serial.print(rxCmd[o], HEX);
        // Serial.print(" ");
    }
    // Serial.print(" | ");

    reData = (value & 0xFF) << 8 | (value >> 8 & 0xFF);

    return reData / 100;
}

int16_t b3mreadInputvoltage(byte id)
{
    byte txCmd[7];
    byte rxCmd[7];
    int16_t value;
    int16_t reData;
    bool flag;

    txCmd[0] = (byte)(0x07); // SIZE
    txCmd[1] = (byte)(0x03); // COMMAND
    txCmd[2] = (byte)(0x00); // OPTION
    txCmd[3] = (byte)(id);   // ID

    txCmd[4] = (byte)(0x4A); // ADDRESS  //現在負荷電流値のアドレス
    txCmd[5] = (byte)(0x02); // LENGTH

    txCmd[6] = 0x00; // SUM

    for (int i = 0; i < 6; i++)
    {
        txCmd[6] += txCmd[i];
        // Serial.print(txCmd[i]);
        // Serial.print("|");
    }
    // Serial.println("");

    txCmd[6] = (byte)(txCmd[6]);
    flag = B3M.synchronize(txCmd, 7, rxCmd, 7);

    if (flag == false)
    {
        return -1;
    }

    // Serial.print("RAM: ");
    for (int o = 4; o < 6; o++)
    {
        value = (rxCmd[o] << 8) | rxCmd[o];
        // Serial.print(rxCmd[o], HEX);
        // Serial.print(" ");
    }
    // Serial.print(" | ");

    reData = (value & 0xFF) << 8 | (value >> 8 & 0xFF);

    return reData / 100;
}
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

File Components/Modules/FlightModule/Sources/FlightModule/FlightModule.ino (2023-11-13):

#include <TaskManager.h>
#include "CANSTM.hpp"
#include "Switch.hpp"
#include "LED.hpp"
#include "DetectionCounter.hpp"
#include "Shiranui.hpp"
#include "Buzzer.hpp"
#include "Camera.hpp"
#include "AnalogVoltage.hpp"
#include "Logger.hpp"
#include "Var.hpp"
#include "FlightModeManager.hpp"
#include "TimeManager.hpp"


namespace internal {
  void task4Hz();
  void task50Hz();
  void task100Hz();

  FlightModeManager flightModeManager;
  TimeManager timeManager;

  namespace flag {
    bool isFalling = false;
    bool isDebugMode = false;
    bool isLaunchMode = false;
    bool isSafeMode = false;
  }
}

namespace device {
  namespace sensor {
    AnalogVoltage supply(A7);
    AnalogVoltage battery(A2);
    AnalogVoltage pool(A3);
  }

  namespace indicator {
    LED canSend(D0);
    LED canReceive(D1);

    Buzzer buzzer(A1, "buzzer");

    LED flightModeBit0(D8);
    LED flightModeBit1(D7);
    LED flightModeBit2(D6);
    LED flightModeBit3(D3);

    void indicateFlightMode(Var::FlightMode mode);
  }

  namespace detection {
    Switch bootSelect1(D12);
    Switch bootSelect2(D5);

    Switch flightPin(D11);

    DetectionCounter liftoffDetector(3);
    DetectionCounter resetDetector(10);
  }

  namespace peripheral {
    Logger logger(D4);
    Camera camera(D9);
    Shiranui sn3(A0, "sn3");
    Shiranui sn4(D13, "sn4");
  }
}


namespace canbus {
  CANSTM can;
}

namespace data {
  float voltageSupply, voltageBattery, voltagePool;
  float motorTemperature, mcuTemperature, current, inputVoltage;
  float currentPosition, currentDesiredPosition, currentVelocity;

  uint32_t performanceMillis;
  float performanceTaskRate;
}


void setup() {
  // デバッグ用シリアルポート
  // internal::flag::isDebugMode = true;
  // Serial.begin(115200);
  // while (!Serial);
  // delay(800);

  internal::timeManager.THRUST_TIME = 1600;
  internal::timeManager.PROTECTION_SEPARATION_TIME = 4200;
  internal::timeManager.FORCE_SEPARATION_TIME = 6900;
  internal::timeManager.DATA_SAVING_TIME = 12120;
  internal::timeManager.LANDING_TIME = 16854;
  internal::timeManager.SHUTDOWN_TIME = 21854;

  // デバッグ中はピンが干渉するので電圧監視を行わない
  if (!internal::flag::isDebugMode) {
    analogReadResolution(12);
    device::sensor::supply.initialize(3300, 750);
    device::sensor::battery.initialize(4700, 820);
    device::sensor::pool.initialize(5600, 820);
  }

  if (!sensor.begin()) {
    Serial.println("失敗したよ");
    while (true);
  }


  SPI.setMOSI(A6);
  SPI.setMISO(A5);
  SPI.setSCLK(A4);
  SPI.begin();

  canbus::can.begin();
  canbus::can.sendEvent(CANSTM::Publisher::FLIGHT_MODULE, CANSTM::EventCode::SETUP);

  // CANで送り損ねないように若干ずらしたレートにする
  Tasks.add(internal::task4Hz)->startFps(5);
  Tasks.add(internal::task50Hz)->startFps(61);
  Tasks.add(internal::task100Hz)->startFps(100);

  internal::flag::isSafeMode = device::detection::flightPin.is(Var::SwitchState::OPEN);
}


void loop() {
  Tasks.update();

  // CAN受信処理
  if (canbus::can.available()) {
    switch (canbus::can.getLatestMessageLabel()) {
    case CANSTM::Label::TRAJECTORY_DATA:
      canbus::can.receiveTrajectoryData(&internal::flag::isFalling);
      device::indicator::canReceive.toggle();
      break;
    case CANSTM::Label::FLIGHT_MODE_ON_COMMAND:
      if (internal::flightModeManager.is(Var::FlightMode::SLEEP)) {
        internal::flightModeManager.changeMode(Var::FlightMode::STANDBY);
        device::peripheral::camera.on();
        device::peripheral::logger.beginLogging();
        device::indicator::buzzer.beepLongOnce();
        canbus::can.sendEvent(CANSTM::Publisher::FLIGHT_MODULE, CANSTM::EventCode::FLIGHT_MODE_ON);
      }

      device::indicator::canReceive.toggle();
      break;
    case CANSTM::Label::RESET_COMMAND:
      if (internal::flightModeManager.is(Var::FlightMode::STANDBY)) {
        internal::flightModeManager.changeMode(Var::FlightMode::SLEEP);
        device::peripheral::camera.off();
        device::peripheral::logger.endLogging();
        device::indicator::buzzer.beepLongOnce();
        canbus::can.sendEvent(CANSTM::Publisher::FLIGHT_MODULE, CANSTM::EventCode::RESET);
      }

      if (internal::flightModeManager.isNot(Var::FlightMode::SLEEP) && internal::flightModeManager.isNot(Var::FlightMode::STANDBY)) {
        internal::flightModeManager.changeMode(Var::FlightMode::SHUTDOWN);
        device::peripheral::camera.off();
        device::peripheral::logger.endLogging();
        device::indicator::buzzer.beepLongOnce();
        canbus::can.sendEvent(CANSTM::Publisher::FLIGHT_MODULE, CANSTM::EventCode::FLIGHT_MODE_OFF, millis());
      }

      device::indicator::canReceive.toggle();
      break;
    case CANSTM::Label::VALVE_MODE: {
      bool isWaitingMode;
      canbus::can.receiveValveMode(&isWaitingMode);
      internal::flag::isLaunchMode = !isWaitingMode;
      device::indicator::canReceive.toggle();
      break;
    }
    case CANSTM::Label::VALVE_DATA_1: {
      canbus::can.receiveValveData1(&data::motorTemperature, &data::mcuTemperature, &data::current, &data::inputVoltage);
      device::indicator::canReceive.toggle();
      break;
    }
    case CANSTM::Label::VALVE_DATA_2: {
      canbus::can.receiveValveData2(&data::currentPosition, &data::currentDesiredPosition, &data::currentVelocity);
      device::indicator::canReceive.toggle();
      break;
    }
    case CANSTM::Label::PERFORMANCE: {
      canbus::can.receivePerformance(&data::performanceMillis, &data::performanceTaskRate);
      device::indicator::canReceive.toggle();
    }
    }
  }
}


/// @brief 4Hzで実行したい処理
void internal::task4Hz() {
  // デバッグ中はピンが干渉するので電圧監視を行わない
  if (!internal::flag::isDebugMode) {
    data::voltageSupply = device::sensor::supply.voltage();
    data::voltageBattery = device::sensor::battery.voltage();
    data::voltagePool = device::sensor::pool.voltage();
  }

  canbus::can.sendVoltage(data::voltageSupply, data::voltagePool, data::voltageBattery);
  device::indicator::canSend.toggle();
}


/// @brief 50Hzで実行したい処理
void internal::task50Hz() {
  // その時のフライトモードに合わせてLEDを切り替える
  device::indicator::indicateFlightMode(internal::flightModeManager.currentMode());


  // CANにデータを流す
  canbus::can.sendSystemStatus(
    internal::flightModeManager.currentMode(),
    static_cast<Var::State>(device::peripheral::camera.get()),
    static_cast<Var::State>(device::peripheral::sn3.get()),
    device::peripheral::logger.isLogging(),
    internal::flightModeManager.isFlying() ? internal::timeManager.flightTime() : -1,
    static_cast<uint8_t>(device::peripheral::logger.getUsage())
  );

  device::indicator::canSend.toggle();
}
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

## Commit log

2023-03-12 標準規格を追加
    [StandardModuleBoard.kicad_pcb, StandardModuleBoard.kicad_sch, StandardModuleBoardShape.dwg]
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2023-03-16 フォルダ構成を変更
    [StandardModuleBoard.kicad_pcb, StandardModuleBoard.kicad_sch, StandardModuleBoardShape.dwg]
2023-03-16 シンボリックリンクを修正
    [StandardModuleBoard.kicad_pcb, StandardModuleBoard.kicad_sch, StandardModuleBoardShape.dwg]
2023-03-16 基板形状を変更
    [StandardModuleBoard.kicad_pcb, StandardModuleBoard.kicad_sch, StandardModuleBoardShape.dwg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]
2023-03-16 シンボリックリンクのパスを修正
2023-03-17 標準モジュール基板のKiCadを追加
    [StandardModuleBoard.kicad_pcb, StandardModuleBoard.kicad_sch]
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2023-03-17 要件定義書を修正
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2023-03-19 標準モジュール基板のREADMEを修正
2023-03-20 試しにPower-Supplyを追加
    [X-H-58-Power-Supply.kicad_pcb, X-H-58-Power-Supply.kicad_sch]
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2023-03-23 基板形状をΦ110に変更
    [StandardModuleBoardShape.dwg, StandardModuleBoardShapeWithSTM.dwg]
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2023-03-25 資料をいろいろ修正
2023-03-25 Projects内へ移動
    [X-H-58-Power-Supply.kicad_pcb, X-H-58-Power-Supply.kicad_sch]
2023-03-25 GNDにpowerflagを追加
    [X-H-58-Power-Supply.kicad_sch]
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2023-03-26 シンボリックリンクの資料を修正
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2023-03-26 標準モジュールの回路図を修正 SPIのプルアップ抵抗難しい。抵抗値は基板製造時にオシロで見るしかない
    [StandardModuleBoard.kicad_sch]
2023-03-27 THRControlModuleBoardの追加
    [THRControlModuleBoard.kicad_pcb, THRControlModuleBoard.kicad_sch, X-H-58-Power-Supply.kicad_pcb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]
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2023-03-27 標準モジュール基板の回路図を修正
    [StandardModuleBoard.kicad_pcb, StandardModuleBoard.kicad_sch]
2023-03-27 標準モジュール基板のボード図を修正
    [StandardModuleBoard.kicad_pcb, StandardModuleBoard.kicad_sch]
2023-03-27 標準モジュール基板のボード図をいい感じに変更
    [StandardModuleBoard.kicad_pcb, StandardModuleBoard.kicad_sch]
2023-03-27 THRControlModuleBoardに熱電対アンプモジュールを追加しました。
    [THRControlModuleBoard.kicad_pcb, THRControlModuleBoard.kicad_sch]
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2023-03-28 THRControlModuleBoardの更新
    [THRControlModuleBoard.kicad_pcb, THRControlModuleBoard.kicad_sch]
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2023-03-28 STM32F303K8のシートを追加
    [STM32F303K8.kicad_sch, THRControlModuleBoard.kicad_pcb, THRControlModuleBoard.kicad_sch]
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2023-03-28 THRControlModuleBoardを更新
    [STM32F303K8.kicad_sch, THRControlModuleBoard.kicad_pcb, THRControlModuleBoard.kicad_sch]
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2023-03-29 標準モジュールにパイロットランプを追加
    [StandardModuleBoard.kicad_pcb, StandardModuleBoard.kicad_sch]
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2023-03-29 計測モジュールのKiCadを追加
    [SensingModuleBoard.kicad_pcb, SensingModuleBoard.kicad_sch]
2023-03-29 StandardModuleBoardからStandardModuleに改名
    [SensingModule.kicad_pcb, SensingModule.kicad_sch, StandardModule.kicad_pcb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]
2023-03-29 Update KiCad
    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
2023-03-29 THRControlModuleBoardにRS485系統を追加しました。
    [STM32F303K8.kicad_sch, THRControlModuleBoard.kicad_pcb, THRControlModuleBoard.kicad_sch]
2023-03-29 通信モジュールを一旦作成
    [SensingModule.kicad_pcb, SensingModule.kicad_sch]
2023-03-29 計測モジュールを一旦作成
    [SensingModule.kicad_pcb, SensingModule.kicad_sch]
2023-03-30 ビアを修正
    [SensingModule.kicad_pcb]
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2023-04-13 スペルミスを修正
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2023-04-18 THRControlModuleを更新
    [THRControlModuleBoard.kicad_pcb, THRControlModuleBoard.kicad_sch]
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2023-04-20 THRControlModule-STM32F303K8の更新
    [STM32F303K8.kicad_sch]
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2023-04-26 フライトモジュールのKiCadを追加
    [FlightModule.kicad_pcb, FlightModule.kicad_sch, SensingModule.kicad_pcb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]
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2023-04-30 バスパワーのピンヘッダをP1.27からP2.54に修正
    [FlightModule.kicad_pcb, FlightModule.kicad_sch]
2023-04-30 バスパワーの接続を修正
    [FlightModule.kicad_pcb, SensingModule.kicad_pcb, SensingModule.kicad_sch]
2023-04-30 RCを解決
    [FlightModule.kicad_pcb, FlightModule.kicad_sch, SensingModule.kicad_pcb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]
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2023-05-01 ミッションモジュールのKiCadを追加
    [MissionModule.kicad_pcb, MissionModule.kicad_sch]
2023-05-01 ミッションモジュール, エアデータ通信モジュール, システムデータ通信モジュールのKiCadを追加
    [AirData.kicad_pcb, AirData.kicad_sch, SystemData.kicad_pcb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]
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2023-05-02 ADXL375のCSをGNDに接続
    [MissionModule.kicad_pcb, MissionModule.kicad_sch]
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2023-05-07 さーぼうごかしたい
    [StandardModuleBoardShape v1.dxf, THRControlModuleBoard.kicad_pcb]
2023-05-07 標準モジュールのdxfファイルを追加
    [StandardModuleBoard_Shape.dxf]
2023-05-07 取付穴位置等を追加
    [THRControlModuleBoard.kicad_pcb, THRControlModuleBoard.kicad_sch]
2023-05-07 不要なファイルを消去
    [StandardModuleBoardShape v1.dxf]
2023-05-08 計測モジュールの基板設計概ね終わり
    [SensingModule.kicad_pcb, SensingModule.kicad_sch]
2023-05-09 計測モジュールとフライトモジュール終わり
    [FlightModule.kicad_pcb, FlightModule.kicad_sch, SensingModule.kicad_pcb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]
2023-05-09 全モジュールのkicadを一通り作った
    [AirData.kicad_pcb, AirData.kicad_sch, FlightModule.kicad_pcb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]
2023-05-09 ソレノイドのサージキラー回路に整流用ダイオードを追加
    [FlightModule.kicad_pcb, FlightModule.kicad_sch]
2023-05-09 ダイオードをSMDに変更
    [FlightModule.kicad_pcb, FlightModule.kicad_sch]
2023-05-09 アルミ殿下を導電性高分子アルミ固体電解コンデンサに変更
    [SensingModule.csv, SensingModule.kicad_pcb, SensingModule.kicad_sch]
2023-05-09 抵抗とLEDを1608に変更
    [SensingModule.kicad_pcb, SensingModule.kicad_sch]
2023-05-09 抵抗値を調整
    [SensingModule.csv, SensingModule.kicad_pcb, SensingModule.kicad_sch]
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2023-05-09 コミットのためにステージ変更
    [THRControlModuleBoard.kicad_pcb]
2023-05-09 リセッタブルフューズをSMDに変更
    [SensingModule.csv, SensingModule.kicad_pcb, SensingModule.kicad_sch]
2023-05-10 一通り部品を選定
    [AirData.csv, AirData.kicad_pcb, AirData.kicad_sch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]
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2023-05-12 KiCADを更新
    [NanoEvery.kicad_sch, THRControlModuleBoard.kicad_pcb, THRControlModuleBoard.kicad_sch]
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2023-05-13 計測モジュールとフライトモジュールのコネクタを再配置
    [FlightModule.kicad_pcb, FlightModule.kicad_sch, SensingModule.kicad_pcb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]
2023-05-14 コネクタを再配置, 基板上で12V->5Vをするように変更
    [AirData.kicad_pcb, AirData.kicad_sch, FlightModule.kicad_pcb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]
2023-05-14 基板設計の都市伝説をいろいろ適応
    [AirData.csv, AirData.kicad_pcb, AirData.kicad_sch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]
2023-05-14 MAX31855、CAN、一部コネクタの追加。 基板形状は供給待ち。
    [NanoEvery.kicad_sch, THRControlModuleBoard.kicad_pcb, THRControlModuleBoard.kicad_sch]
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2023-05-14 PCBにQRコードを追加
    [NanoEvery.kicad_sch, THRControlModuleBoard.kicad_pcb, THRControlModuleBoard.kicad_sch]
2023-05-14 BOMを追加
    [THRControlModuleBoard.csv]
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2023-05-15 裏面にQRコードと署名を追加
    [AirData.kicad_pcb, FlightModule.kicad_pcb, MissionModule.kicad_pcb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]
2023-05-15 ロゴを修正
    [FlightModule.kicad_pcb]
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2023-05-18 計器マウントプレートの穴径をタカチのケーブルグランドにあわせて修正
    [AvionicsMountPlate.kicad_pcb, AvionicsMountPlate.step]
2023-05-18 カメラの制御回路を修正
    [FlightModule.csv, FlightModule.kicad_pcb, FlightModule.kicad_sch]
2023-05-18 ソレノイドのサージ対策回路を修正
    [FlightModule.csv, FlightModule.kicad_pcb, FlightModule.kicad_sch]
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2023-05-20 ベタを修正
    [AirData.kicad_pcb, FlightModule.kicad_pcb, MissionModule.kicad_pcb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]
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2023-05-21 MSOPの3Dモデルを修正
    [Power.kicad_pcb]
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2023-05-21 変圧基板の値を修正
    [Power.kicad_pcb, Power.kicad_sch]
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2023-05-21 領域侵犯禁止領域を修正
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2023-05-23 許されざる基板を修正
    [AvionicsMountPlate.kicad_pcb, AvionicsMountPlateJoke.kicad_pcb, Transformation.kicad_sch]
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2023-05-29 構造を微修正
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2023-06-08 ブザーの回路を修正
    [FlightModule.kicad_pcb, FlightModule.kicad_sch]
2023-06-08 電磁弁制御のフォトカプラの位置を修正
    [FlightModule.kicad_pcb, FlightModule.kicad_sch]
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2023-06-10 姿勢角の符号を修正
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2023-06-11 なぜか受信切り替えをコメントアウトしてた。 送信したのはいいが受信を一切受け付けないツンツンモードになっていたため修正。
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2023-06-12 配線の繋ぎ忘れを修正
    [AirData.kicad_pcb, AirData.kicad_sch, MissionModule.kicad_pcb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]
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2023-06-14 スカラ値のデシリアライズを修正
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2023-06-19 計器チューブ図面の値を修正
2023-06-19 分離制御回路を修正
    [FlightModule.csv, FlightModule.kicad_pcb, FlightModule.kicad_sch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]
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2023-06-19 追加修正
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2023-06-19 漢字間違え修正
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2023-06-20 分離制御の論理回路図を修正
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2023-06-26 🐛 memcpyのポインタを、ミスっていたので修正
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2023-06-27 🎨 無駄にスネークケースだったことろをキャメルケースに修正
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2023-06-28 CAN受信LEDの点滅タイミングを欲しいパケットを受信した時のみに修正
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2023-07-03 🐛 CAN受信処理のラベルを修正
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2023-07-03 💬 READMEの参照気圧設定コマンドのデータ長をミスっていたので修正
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2023-07-05 ♻️ 余計な個所を微修正
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2023-07-08 🐛 ログ保存OFFの状態で起動するように修正
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2023-07-10 Revert "🚧 バッテリー切れ(死)"
    This reverts commit 6ca955eedc5a3f155d30bc1fa7058b48da335df3.
    [SensingModule.ino]
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2023-07-10 ✏️ 変数名の誤字を修正
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2023-07-11 頂点検知試験用のモックデータを20Hzに修正
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2023-07-12 🐛 FRAMをクリアする前に書き込み位置をリセットするように修正
2023-07-12 🐛 FRAMの容量を超えていてもSDへは書き込むように修正
2023-07-12 🐛 FRAMのクリアの前にライトイネーブルが設定されていなかった問題を修正
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2023-07-12 💡 Buzzerにコメントを追加
2023-07-12 🐛 ブザーをトグルする前にOFFにするように修正(一生なり続ける問題解消)
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2023-07-13 🐛 SDが不正でもログ開始はするように修正
2023-07-13 SwitchのOPENとCLOSEが逆だったので修正
2023-07-13 ⚡️ パフォーマンス改善のためログ保存開始時にSDが認識できない時は初期化しないように修正
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2023-07-13 🐛 Varを使った実装に修正
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2023-07-13 🐛 CAN受信を修正
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2023-07-22 🐛 姿勢角と偽って地磁気を送信していた問題を修正
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2023-07-25 🐛 電圧をCAN送信の引数が間違っていたので修正
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2023-07-26 🐛 座標軸を修正
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2023-07-31 姿勢角を修正
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2023-08-02 🐛 SN4のピンをSN3として使うことで、分離中ログが保存されていなかった問題を修正
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2023-08-04 🐛 不正なデータを弾けるように修正
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2023-08-04 🚑 長時間放置した場合FRAMの書き込み位置がリセットされる問題を修正
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2023-08-05 🐛 ADXLの出力を修正
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2023-08-06 lsbを修正
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2023-08-07 📝 READMEの見出しを修正
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2023-08-17 FRAMを使えない問題を修正
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2023-08-18 ADXLを修正
2023-08-18 温度の受信を修正
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2023-09-24 3dモデルを修正
    [THRControlModule.kicad_pcb]
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2023-09-24 修正したバルブシステムのブロック図を追加
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
